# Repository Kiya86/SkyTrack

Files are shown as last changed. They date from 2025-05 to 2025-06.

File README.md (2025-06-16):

# SkyTrack
FPV drone project that can hopefully reach 100 mph with carbon reinforced 3d printed frame. This drone has been an idea of mine for a couple of years now, but due to funding issues, it never really got finalized. I thank Hack Club for making this possible. 

All of the parts I sourced are on AliExpress to keep the cost of the drone down. When comparing to other sources, I found out I can save a lot lol. 

BOM:

| Parts | Exact Name | Store (Tried to keep the same)| Qty |Price | Shipping  | Total |
|---|---|---|:---:|---|---|---|
| ESC (4-in-1) | [3065 AM32 32-Bit 65 A 3–8 S ](https://www.aliexpress.us/item/3256808309426590.html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) | RC Model DIY Space Store (Trader) |  1  | $60.29 | Free | $60.29 |
| FPV Camera |[ RunCam Night Eagle 3 V2 1500TVL  ](https://www.aliexpress.us/item/3256805455115288.html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)| Hobbyfpv Store (Trader) |  1  | $49.37 | Free | $49.37 |
| Receiver | [TBS Crossfire Nano SE (915/868 MHz)](https://www.aliexpress.us/item/3256808530734463.html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) | Ajuan Aviation Model Store Store (Trader) |  1  | $40.15 | Free | $40.15 |
| Motor Wires |[ Silicone 18 AWG, 5 m (Blue) ](https://www.aliexpress.us/item/3256802725059624.html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) | MUCG Official Store (Trader) |  1  | $12.44 | Free | $12.44 |
| Power Wires (Black) | [Silicone 12 AWG, 1 m (Black) ](https://www.aliexpress.us/item/3256802725059624.html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) | MUCG Official Store (Trader) |  1  | $11.30 | Free | $11.30 |
| Power Wires (Red) | [Silicone 12 AWG, 1 m (Red) ](https://www.aliexpress.us/item/3256802725059624.html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) | MUCG Official Store (Trader) |  1  | $11.30 | Free | $11.30 |
| Motors | [Axisflying Bando 2207.5, 1960 KV, 6 S  ](https://www.aliexpress.us/item/3256806145330407.html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) | Freaking RC Store (Trader) |  4  | $85.66 | $1.83 | $87.49 |

Summary (Provided on AliExpress)
- Parts Total: $272.34  
- Shipping Total: $11.78 
- Additional charges: $26.19  
- Total: $306.44


FullDroneChassis


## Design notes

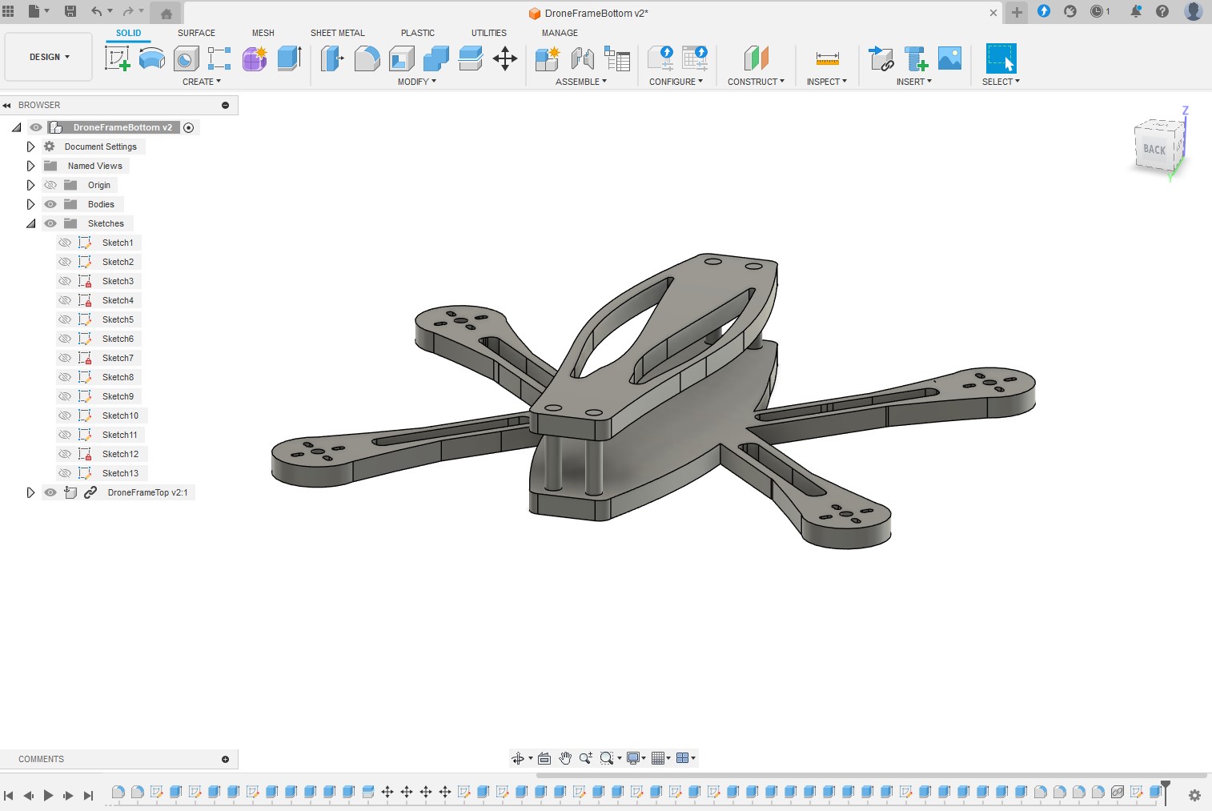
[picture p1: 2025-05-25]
src/CAD/FullDroneChassis.jpg

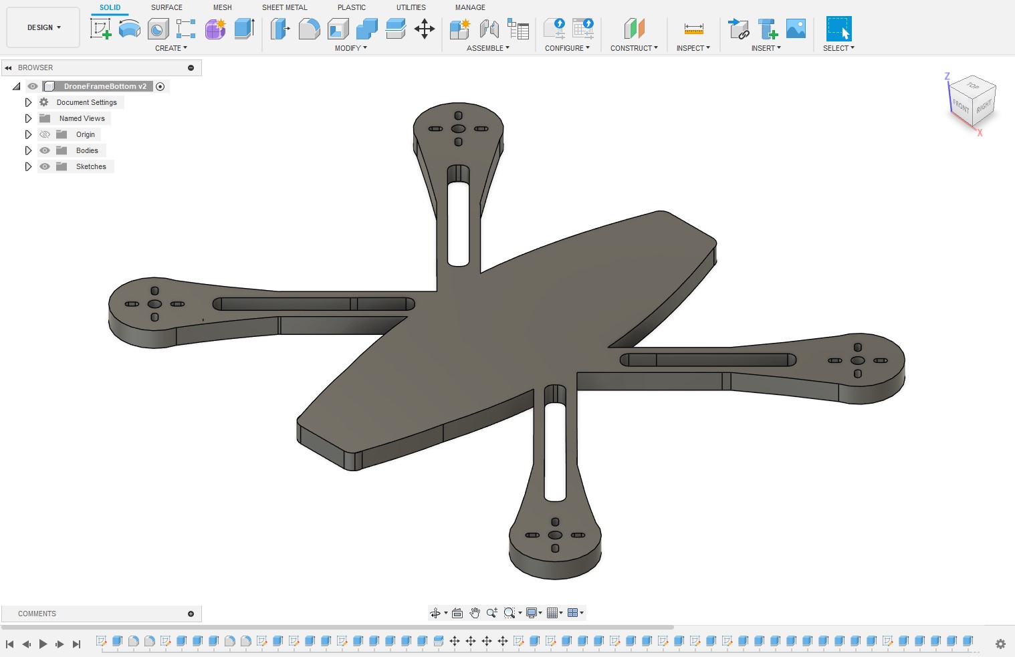
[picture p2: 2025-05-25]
src/CAD/BottomDrone.jpg

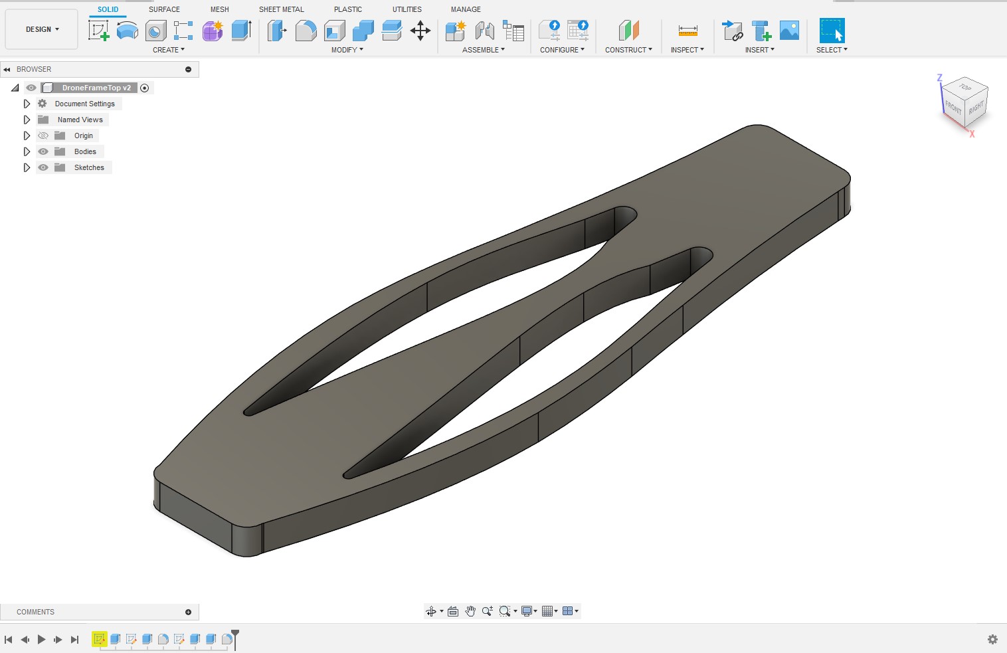
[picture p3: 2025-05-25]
src/CAD/TopDrone.jpg

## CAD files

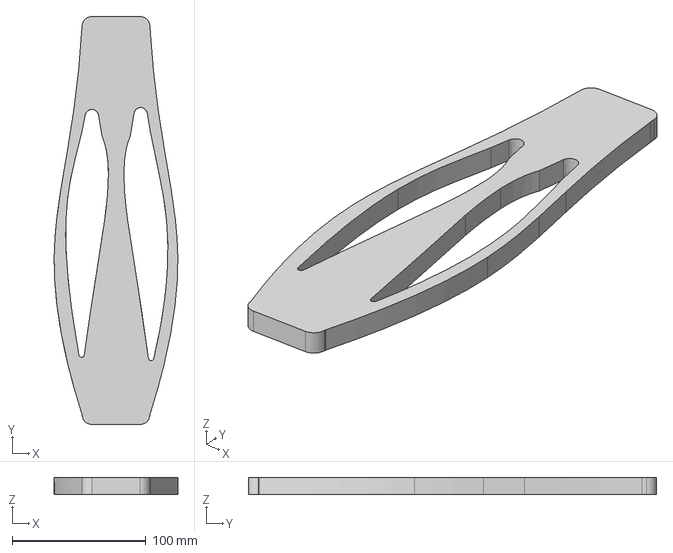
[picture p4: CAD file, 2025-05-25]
src/CAD/DroneFrameTop.step
92.5 x 304.8 x 12.7 mm

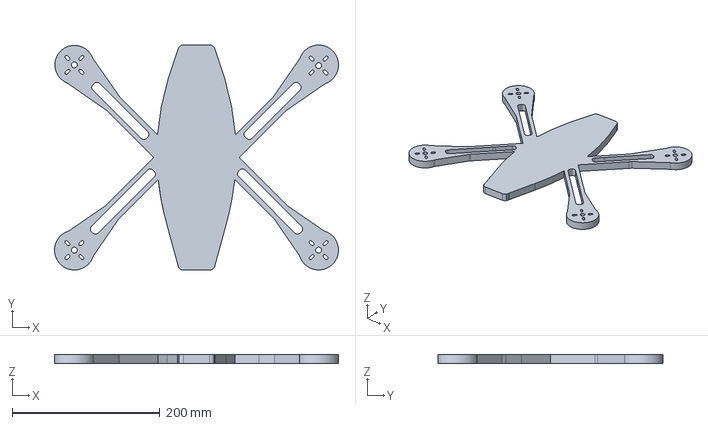
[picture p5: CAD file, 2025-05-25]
src/CAD/DroneFrameBottom.step
384.8 x 304.8 x 12.7 mm

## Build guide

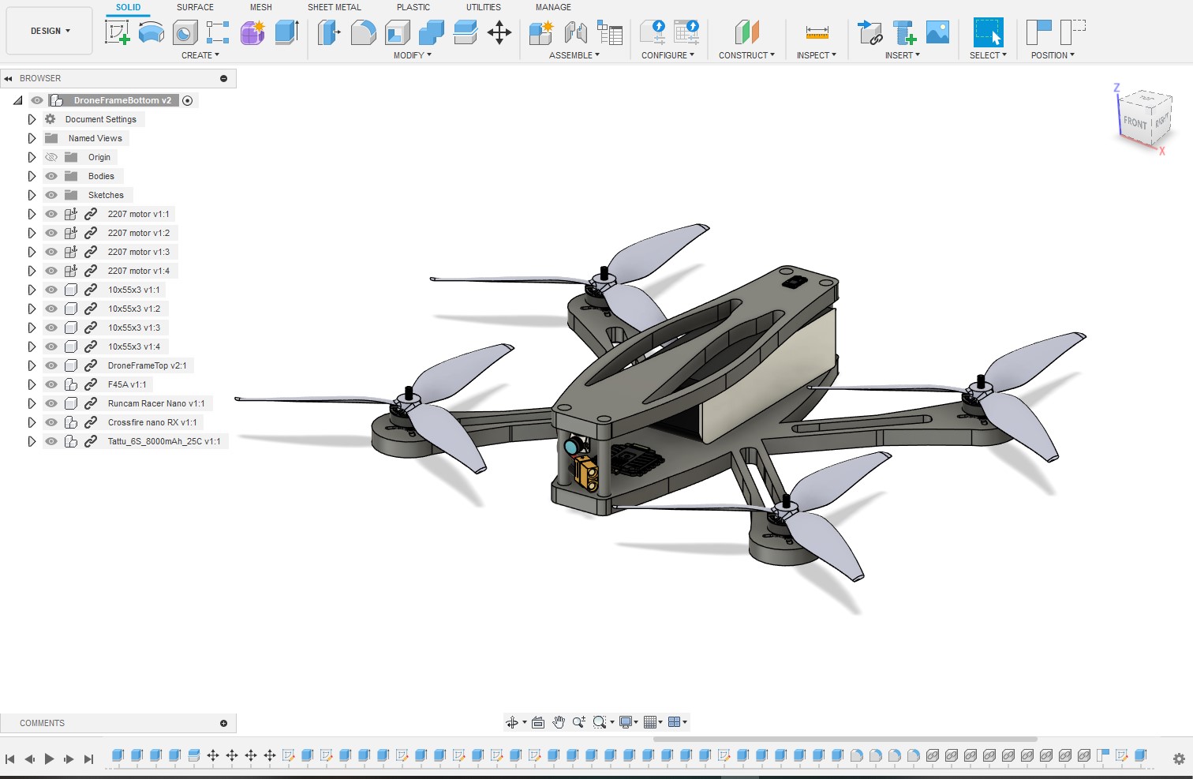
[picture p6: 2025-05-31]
src/CAD/AssembledDrone.jpg

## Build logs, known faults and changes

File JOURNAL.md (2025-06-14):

---
title: "SkyTrack"
author: "Kiya Kesheh"
description: "100 mph FPV drone!
created_at: "2025-05-21"
---

## **Day 1** (05/21/2025)

* Did research on what components are best  
  * Compared thrust, KV, and RMP curves for multiple 5-inch prop motors   
  * Selected the:  
    *  Axisflying Bando 2207.5 1960 KV motors based on their torque and top-end RPM on 6 S  
  * Also chose a 65A 4 in 1 ESC for the motors  
    * 3065 AM32 65 A 4-in-1 ESC  
  * Compared flight controllers to see what is best and whether I should use F7 flight computers, but instead opted to use the F4 flight computer  
    * Matek F405-HDTE  
      * Has an STM32F405  
      * MPU6000  
      * Onboard OSD  
      * And built a current sensor   
  * Also did research on what propeller size I should be using and decided a 5-inch is best for a high-speed drone, so I chose:  
    * HQProp Ethix S4 5×4.5×3 tri-blades  
  * Also decided to use a 6S battery as the motors would run at max speed with it  
    * 2pcs CNHL Lipo Battery 6S 22.2V 1100mAh 1500mah 100C With XT60 For RC FPV Quadcopter Airplane Helicopter Hobby  
    *   
* Lastly made a BOM of all parts to see how much it would cost, and the exact price with tax and shipping is **$304.20**

## **Day 2** (05/22/2025)

* Made a sketch of a frame to work with the 5-inch props and made sure the center of gravity would not be messed up   
* Drew the sketch in Fusion 360 and made a 240mm diameter motor-to-motor spacing  
* Modeled the body with channels to route wires going from the ESC to the motors   
* Added other channels to hide wires   
* Added a low-profile canopy   
* Did not add mounting holes, as I will be using a soldering iron with brass inserts   
* Beefed up sections under high loads
  
Made the sketch for the drone frame 

 
 
Did some shaping via sketches 



Extended the frame to fit the props and to clear the battery 



Making the top portion of the drone using the bottom sketch 

 
 
Did some weight using another sketch 

 
 
Rounded corners to make it look nicer

 

## **Day 3** (05/23/2025)

* Fixed some geometry of the drone and reduced weight  
* Added more channels for battery wires  
* Started to make the GitHub repository (This was done a little later the day after (I might or might not have feel asleep))
* Added all parts to an Excel sheet and saw how much tax and shipping fees were on Aliexpress  
* Added everything to the BOM and finalized last-minute changes  
* 3D printed the frame with carbon reinforced filament (Nozzle is cooked)   
* The frame was printed at:  
  * Nozzle: 230 °C  
  * Bed: 100 °C  
  * Infill: Gyroid at 50% infill   
  * 0.2mm layers   
  * Speed: 75%   
  * Slicer: Cura

 ## **My Story** 

* Ever since I started my sophomore year of high school, I have wanted to take on a project that was ambitious. After months of brainstorming, I came up with a couple of ideas, such as building a rover, a high-speed drone, or rockets. After debating and consulting my sibling, I decided to watch videos on drone builds, and I was amazed! All of the parts available and the electronics just shocked me. How did they think of this? How was this made? After countless videos, I came up with a rough list of requirements: carbon frame, high-kv motors, all-in-one ESC, 4s lipo, lightweight, and cool paint job. After adding up the costs of all parts, I found it to be very expensive, as all parts totaled $500. This was way too much and still is way too much for my family (low income), so I decided to put the entire project to the side and build rockets instead (Way cheaper). But after getting bored of rockets, I came back to the drone project due to "highway" and decided to update the parts and reduce costs as I could reuse what I had. For example, I have a 6s lipo, so I adapted the ESC to that and got rid of the battery (4s one). The total cost for the new BOM proved to be way less, and has got me excited, as I have a plan for this drone that I will hopefully build.
* 
